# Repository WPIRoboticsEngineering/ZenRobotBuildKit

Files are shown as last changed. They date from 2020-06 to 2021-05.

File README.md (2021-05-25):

# ZenRobotBuildKit

Zen robotics build kit is a robot build system. Here are the BOM and CAD models.


 

# Set Up An IDE

Instructions for setting up an IDE will be provided in class.

# Build the Romi

Instructions will be provided in class.

# RBE1001Lib Documentation

[RBE1001Lib Doxygen page](https://wpiroboticsengineering.github.io/RBE1001Lib/annotated.html)

# BOM Source

## Tools Kit (Online only, suggested)
  
  1 x wire stripper https://www.pololu.com/product/1923
  
  1 x Digital Multi Meter https://www.sparkfun.com/products/12966
  
  1 x soldering iron  https://www.sparkfun.com/products/14456
  
  1 x soldering stand  https://www.sparkfun.com/products/9477
  
  1 x spool of solder lead free https://www.digikey.com/product-detail/en/aven-tools/17551LF/243-1341-ND/5252791
  
  1 x spool of solder wick https://www.sparkfun.com/products/9327
  
  1 x spring scale https://www.elexp.com/71ea7-g63spring-scale-tubular-5000g-yel.html
  
  1 x x86_64 PC running Windows or Linux nativly
  * No MacOS (install windows dual-boot)
  * No Chromebooks (No way to get the software working)
  * No Microsoft Surfaces (if they are the ARM variant)

## Consumables Kit 

  Note that students only need a portion of the items here: e.g., they don't each need a wire spool kit -- they just need enough wire to wire their 'bot.

  1 x pack of zipties https://www.amazon.com/Cable-Nylon-Locking-Pieces-Black/dp/B07VRSQ6YL
  
  1 x roll double sided tape Foam tape https://www.amazon.com/Scotch-Mounting-0-75-inch-350-inches-110-LongDC/dp/B009NP1OBC
  
  1 x Wire Kit https://www.amazon.com/REXQualis-Breadboard-Assorted-Prototyping-Circuits/dp/B081H2JQRV
  
  1 x Wire spool kit https://www.amazon.com/StrivedayTM-Solid-Electric-gauge-26-2ft/dp/B077HRKYB1
  
  ```alternate   https://www.mouser.com/ProductDetail/Adafruit/1311?qs=GURawfaeGuBbUKgxUfZ%252BxQ%3D%3D```

## ESP32 Processor Kit CD-2021

1 x ESP32-DevKitC-VB https://www.digikey.com/product-detail/en/espressif-systems/ESP32-DEVKITC-32D/1965-1000-ND/9356990

1 x ZenDriver board (Provided by B Star contract manufacturer) https://shop.bstarengineering.com/

1 x USB cable https://www.amazon.com/NetDot-Magnetic-Charging-Transfer-Compatible/dp/B07QDS3CHN bought in packs of 3

1 x Breadboard https://www.pololu.com/product/4000 (specifically this one, as it has mounting holes)

## ESP32 Processor Kit AB-2020

  1 x ESP32-DevKitC-VB https://www.digikey.com/product-detail/en/espressif-systems/ESP32-DEVKITC-32D/1965-1000-ND/9356990
  
  1 x USB cable https://www.amazon.com/NetDot-Magnetic-Charging-Transfer-Compatible/dp/B07QDS3CHN bought in packs of 3

  1 x Breadboard https://www.pololu.com/product/4000 (specifically this one, as it has mounting holes)
  
  1 x #3543 Motor Driver and Power Distribution Board for Romi Chassis = 19.95
  
  7 x Zener Diode https://www.digikey.com/products/en?keywords=BZX55B3V9-TAPGICT-ND
  
  3 x 1x06 Male Header https://www.digikey.com/products/en?keywords=2057-PH1-06-UA-ND
  
  2 x 1x03 Female Header https://www.digikey.com/product-detail/en/sullins-connector-solutions/PPPC031LFBN-RC/S7036-ND/810175
  
  2 x 1x04 Male Header https://www.digikey.com/products/en?keywords=%202057-PH1-04-UA-ND
  
  4 x 1x19 Female Header https://www.digikey.com/products/en?keywords=PPTC191LFBN-RC
  
  1 x 1x02 male header https://www.digikey.com/product-detail/en/adam-tech/PH1-02-UA/2057-PH1-02-UA-ND/9830266
  
  1 x 1x04 Female Header https://www.digikey.com/product-detail/en/sullins-connector-solutions/PPPC041LFBN-RC/S7037-ND/810176
  
  1 x 1x03 Male Header https://www.digikey.com/product-detail/en/sullins-connector-solutions/PREC003SAAN-RC/S1012EC-03-ND/2774851
  
  1 x Romi Battery Contact Set https://www.pololu.com/product/3540

  1 x 1 kOhm resistor (reassigned from Sensors Kit -- only needed for shim board)
  
  1 x jumper

  1 x Custom PCB https://github.com/WPIRoboticsEngineering/1001-romi-processor-shim
  
```
  This will be produced and provided by the Robotics Department 
  ```

## 32u4 Processor Kit

  1 x Romi 32U4 Control Board https://www.pololu.com/product/3544
  
  3 x 1x6 socket: https://www.pololu.com/product/1016
  
  2 x 1x9 socket: https://www.pololu.com/product/1019 (2001 students: you'll also need the 3rd 1x9 socket in the Sensors Kit.)
  
  1 x 1x40 breakaway pins: https://www.pololu.com/product/1065
  
  1 x USB cable https://www.amazon.com/NetDot-Magnetic-Charging-Transfer-Compatible/dp/B07QDS3CHN bought in packs of 3

  1 x Breadboard https://www.pololu.com/product/4000 (specifically this one, as it has mounting holes)
  
  1 x Side-entry screw terminal: https://www.pololu.com/product/2491 (comes in packs of three -- each kit needs one)

## Chassis Kit

  1 x #3660 Romi Chassis Kit/Encoders (BULK special purchase)
  ```
  Low volume alternate source 
  
   1 x chassis kit https://www.pololu.com/product/3501
   1 x Romi Encoder Pair https://www.pololu.com/product/3542
  
  ```
  
  1 x #3560 Romi Chassis Expansion Plate - Black = 4.75
  
  1 x #3531 Romi Chassis Ball Caster Kit = 2.95 (color unimportant)
  
  1 x #1944 Aluminum Standoff: 1 1/4", 2-56 thread (4-pack): https://www.pololu.com/product/1945
  
  1 x #1943 Aluminum Standoff: 3/4", 2-56 thread (4-pack): https://www.pololu.com/product/1943

  1 x #2009 Aluminum Standoff: 1 1/2", 2-56 thread (4-pack): https://www.pololu.com/product/2009
  
  1 x 2-56 nut set https://www.pololu.com/product/1067
  
  1 x 2-56 x 1/4"long https://www.pololu.com/product/1955   

  1 x Servo with feedback https://www.pololu.com/product/3436
  
  1 x 2-56x 1.25" https://www.mcmaster.com/90272A087
  
  10 x 2-56x 3/4" https://www.mcmaster.com/90272A084
  
## Sensors Kit
  
  1 x line sensor array (6 x 8mm): https://www.pololu.com/product/4246
  
  1 x ultrasonic https://www.sparkfun.com/products/15569 
  
  1 x wire for ultrasonic https://www.sparkfun.com/products/10369

  2 x photoresistor: https://www.sparkfun.com/products/9088
  
  1 x yellow LED
  
  1 x 330 Ohm resistor

  2 x 2.2 kOhm resistor
  
  (1) 1x9 socket: https://www.pololu.com/product/1019 
  
  1 x potentiometer Digikey PN 3310R-125-103L-ND
  
  1 x IR receiver: https://www.pololu.com/product/2471 

  1 x IR remote: https://www.pololu.com/product/2777
  
## 2001 Add On kit

 1 x Motor With Encoder https://www.sparkfun.com/products/16413
 
 1 x Motor Driver - Dual TB6612FNG https://www.sparkfun.com/products/14450
 
 1 x transistor Digikey https://www.digikey.com/en/products/detail/on-semiconductor/2N2222/33077
 
 1 x relay Electronix Express PN: 22RCLR5V
  
 1 x Diode digikey 	1N4007-TPMSTR-ND
 
## 2002 Add On Kit
 
 1 x Cable for Sharp IR sensor: https://www.sparkfun.com/products/13685
 
 1 x SharpIR bracket https://www.pololu.com/product/2677
 
 1 x SharpIR proximity sensor https://www.pololu.com/product/136
  
 <!--(tentative) 1 x ToF distance sensor: https://www.pololu.com/product/2490-->

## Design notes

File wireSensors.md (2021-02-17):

# Ultrasonic Range Finder

## V3 boards

The shim board comes with a 4-pin port for connecting your ultrasonic sensor. Using your 4-wire cable connect the sensor to the port. Common practice is to use green for GND and red for power, which matches nicely with the cable.

Unfortunately, due to an oversight (from a change in ESP32 version), the pins that are wired to the ultrasonic don't have the necessary functionality, so you'll need to add wires to connect pin 16 to pin 22 and pin 17 to pin 23. You can just use the sockets in the shim board.

## v2 boards

Vcc to 5vv/VUSB

Gnd to Gnd

Echo to One side of a 2.2k resistor

The other side of the 2.2k Resistor to GPIO 22

Trig to GPIO 23

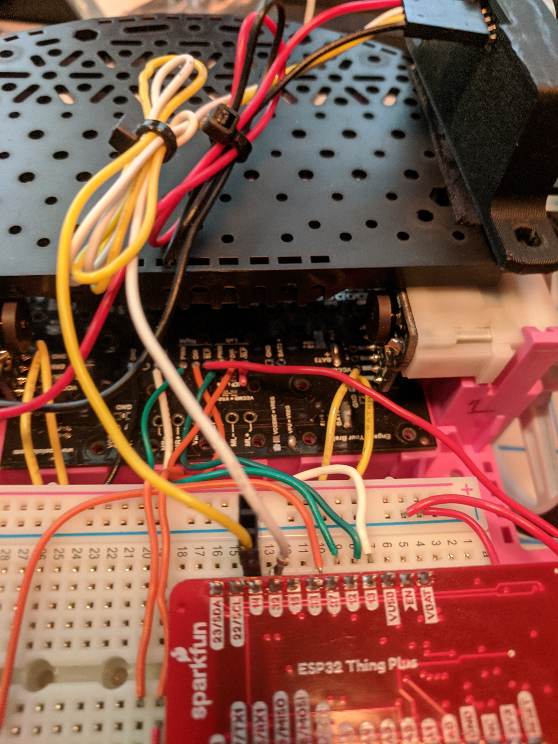
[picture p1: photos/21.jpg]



# Line Sensors

Your shim board has two 3-pin connectors for line sensors. The arrangement is set up to work with individual line sensors, but it will also work with the line sensor array.

Connect the '3V' terminal from one of the line sensor sockets to Vcc on the sensor array. Connect 'GND' to GND. You do not need to connect the '3V' and 'GND' from the other set of pins.

Connect the middle pin of each 3-pin socket to your choice of sensor elements: labelled 1, 3, 5, 7, 9, or 11 on the sensor array. These correspond to each of the physical sensors on the working side of the sensor array. In the end, you'll want to choose two sensors that are roughly the width of the piece of tape you use for line following, but you can easily try different sensor elements. The sockets are connected to pins 36 (A4) and 39 (A3) on your ESP32.

# Servo

The shim board has a 4-pin connector for the servo. Connect the black wire (ground) on the servo cable to the '-' terminal. The red wire will connect to 5V and the white to the signal line (pin 33). Connect the green feedback wire to the last pin, pin 34 (A2).

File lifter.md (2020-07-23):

# Build the Lift mechanism

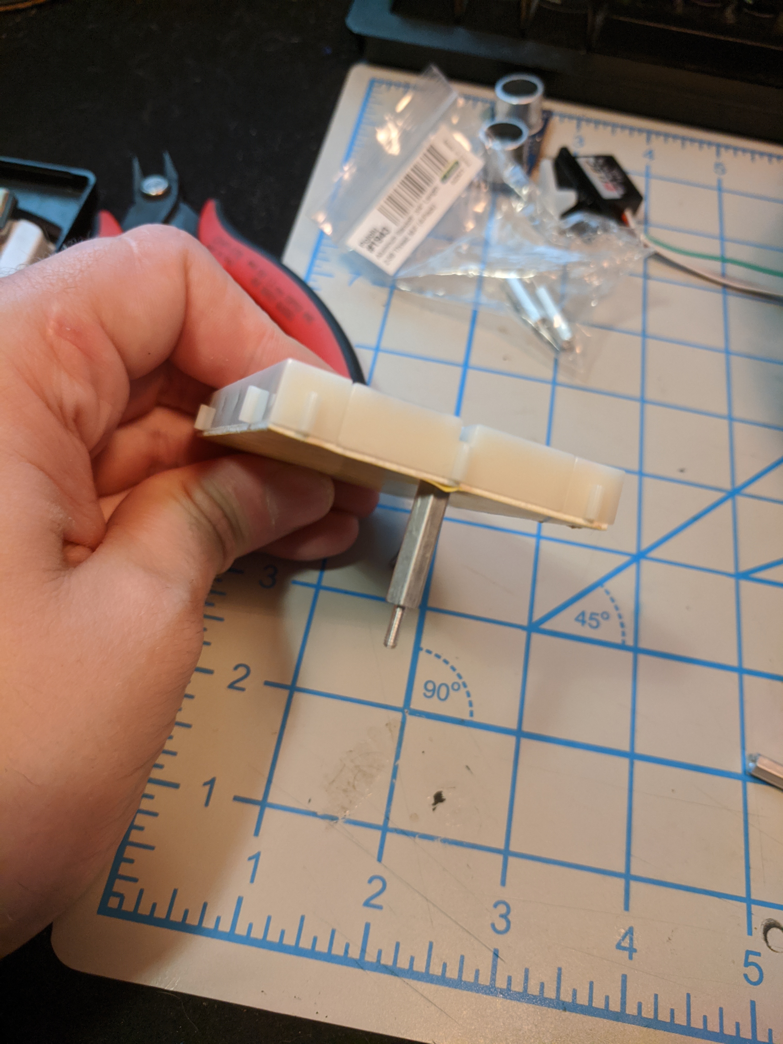
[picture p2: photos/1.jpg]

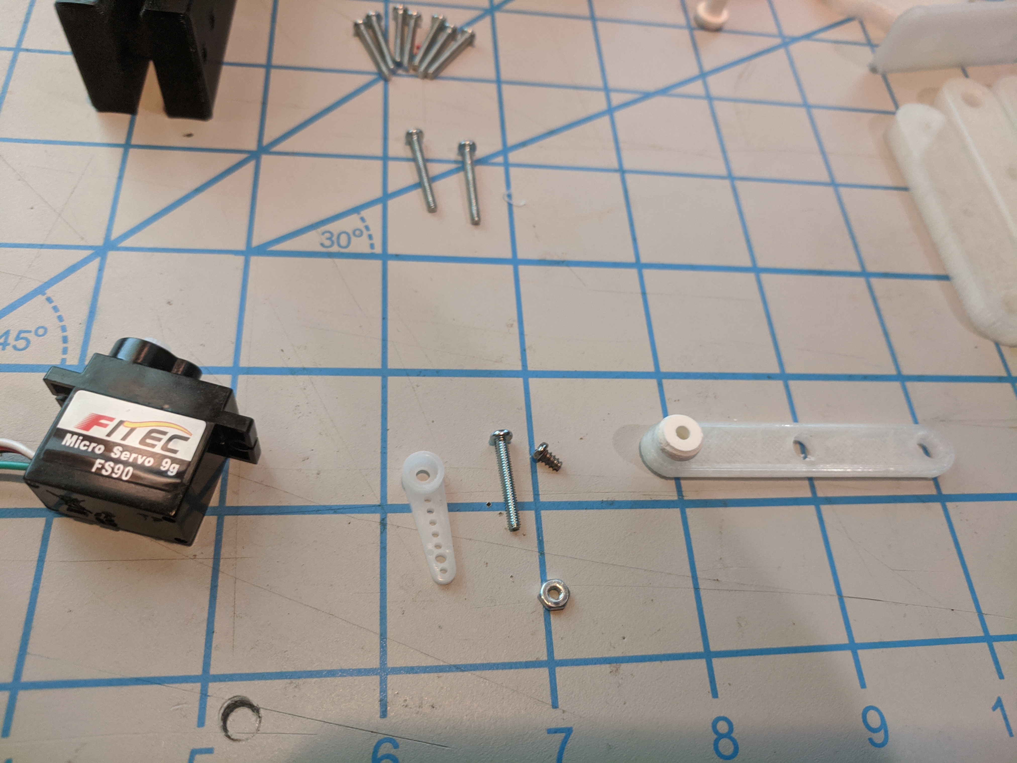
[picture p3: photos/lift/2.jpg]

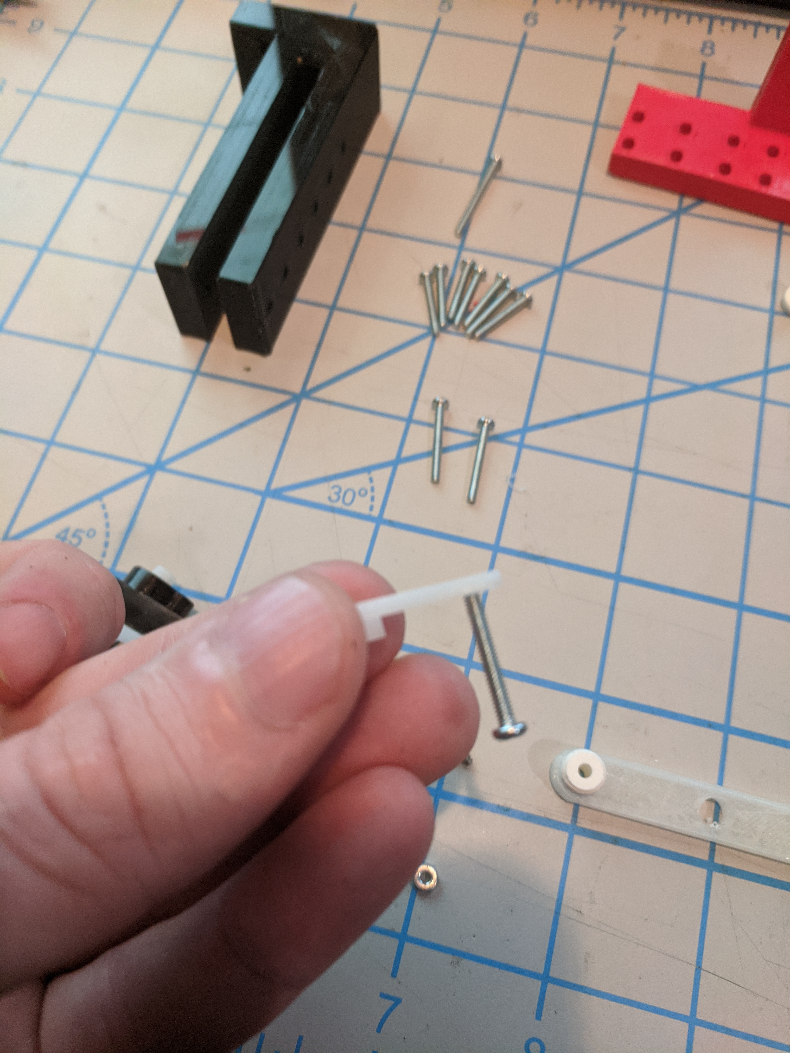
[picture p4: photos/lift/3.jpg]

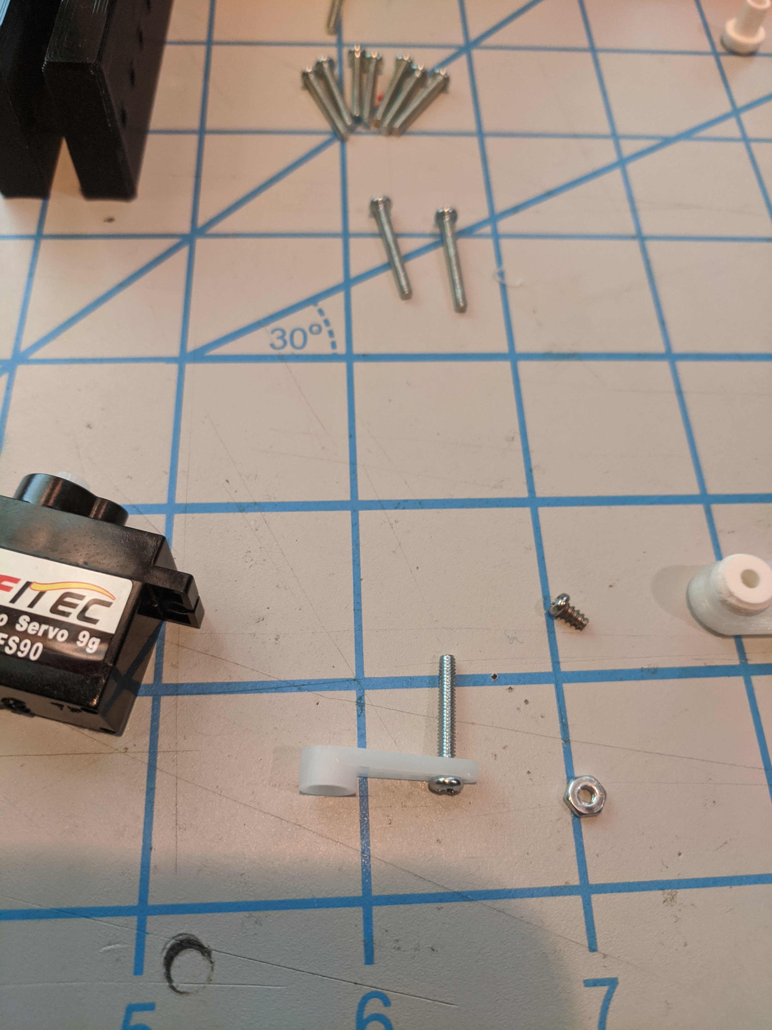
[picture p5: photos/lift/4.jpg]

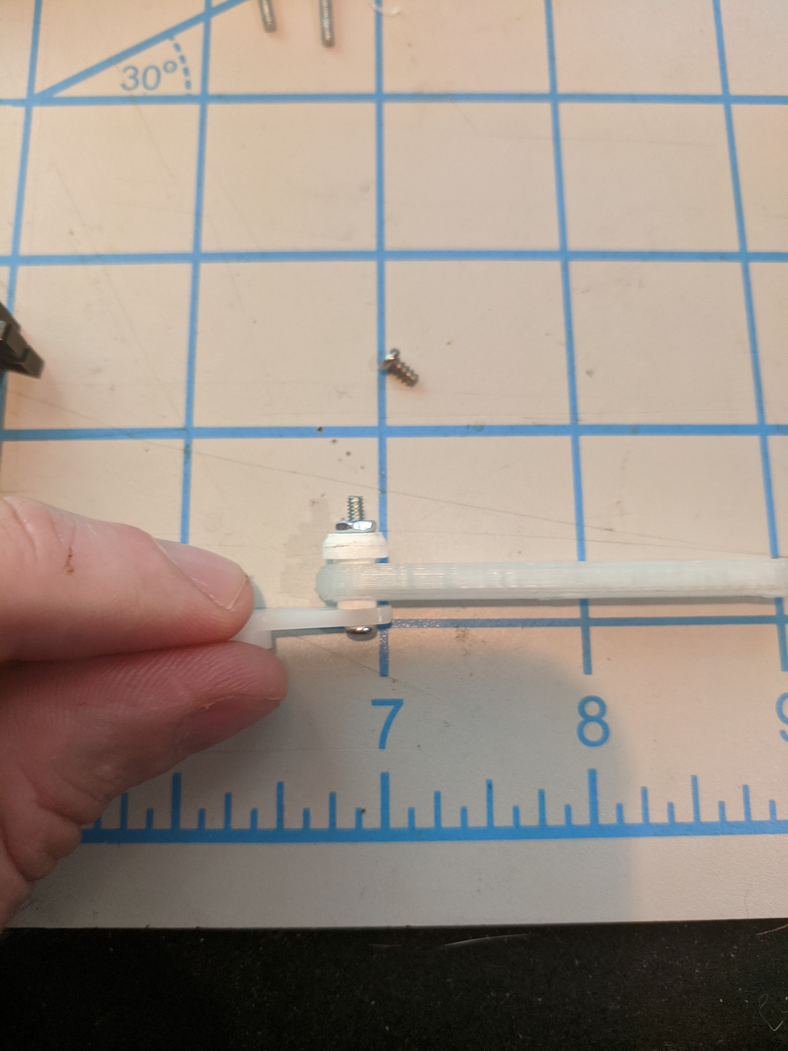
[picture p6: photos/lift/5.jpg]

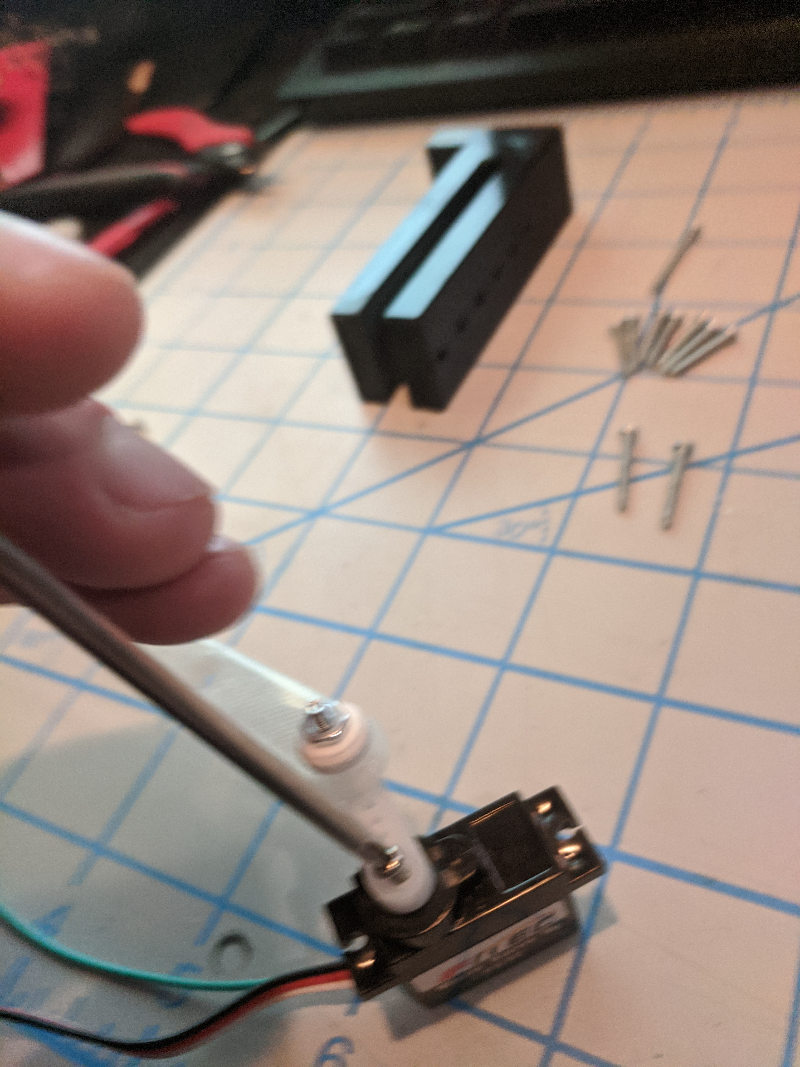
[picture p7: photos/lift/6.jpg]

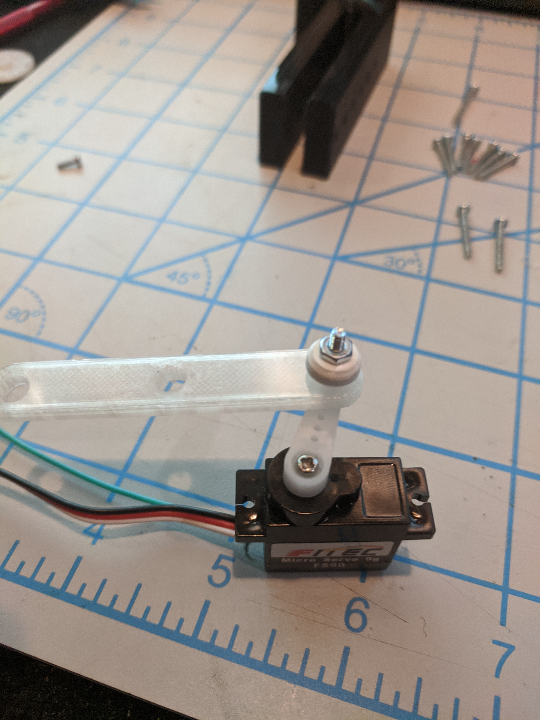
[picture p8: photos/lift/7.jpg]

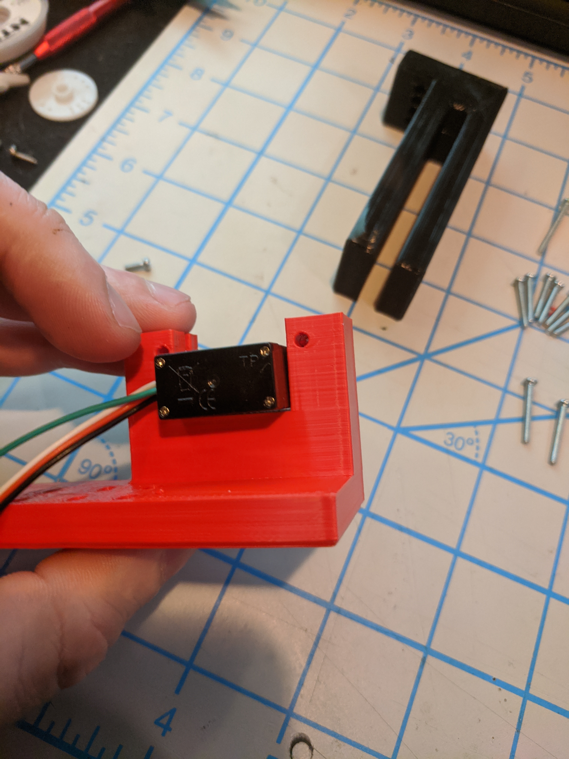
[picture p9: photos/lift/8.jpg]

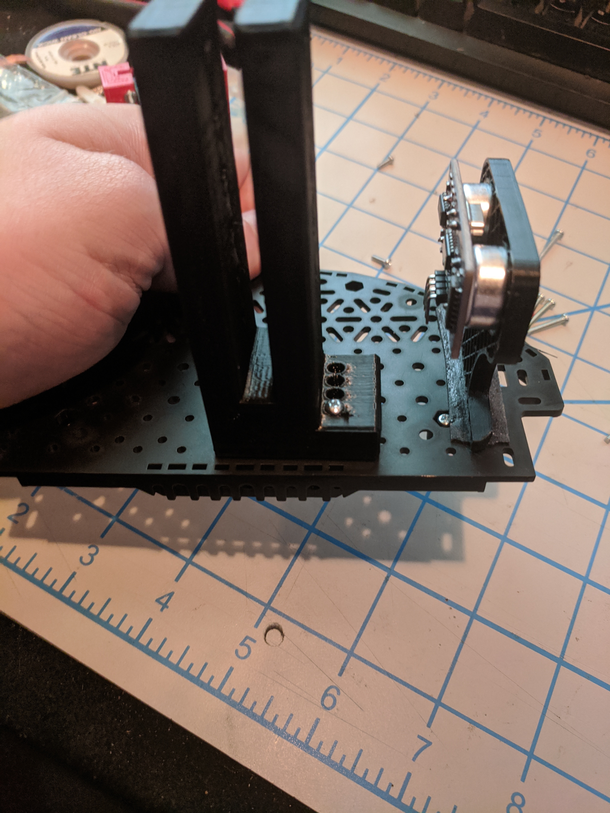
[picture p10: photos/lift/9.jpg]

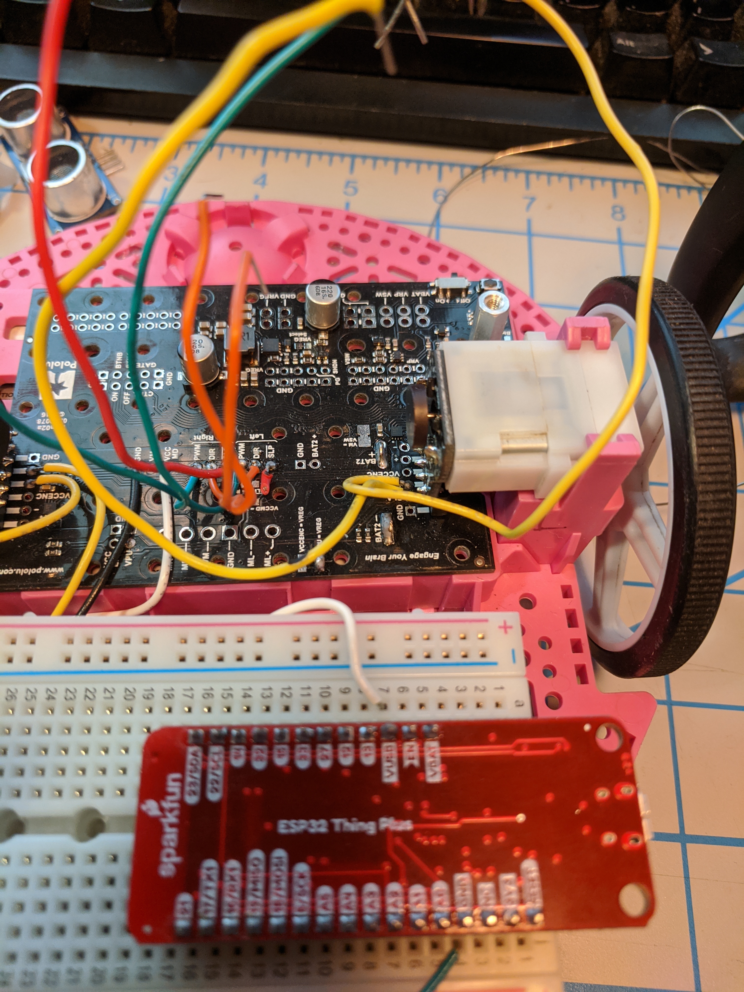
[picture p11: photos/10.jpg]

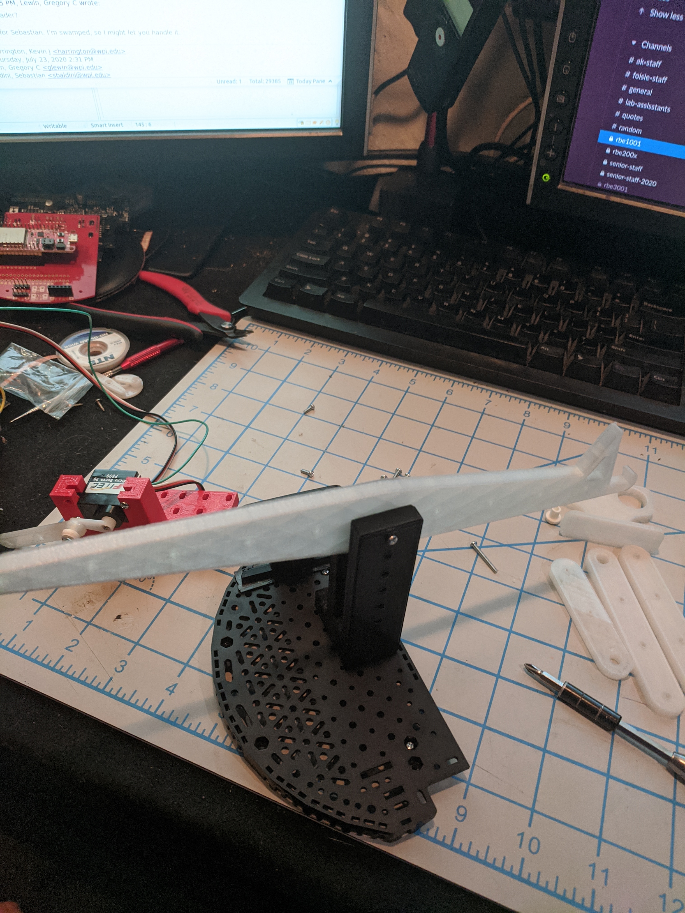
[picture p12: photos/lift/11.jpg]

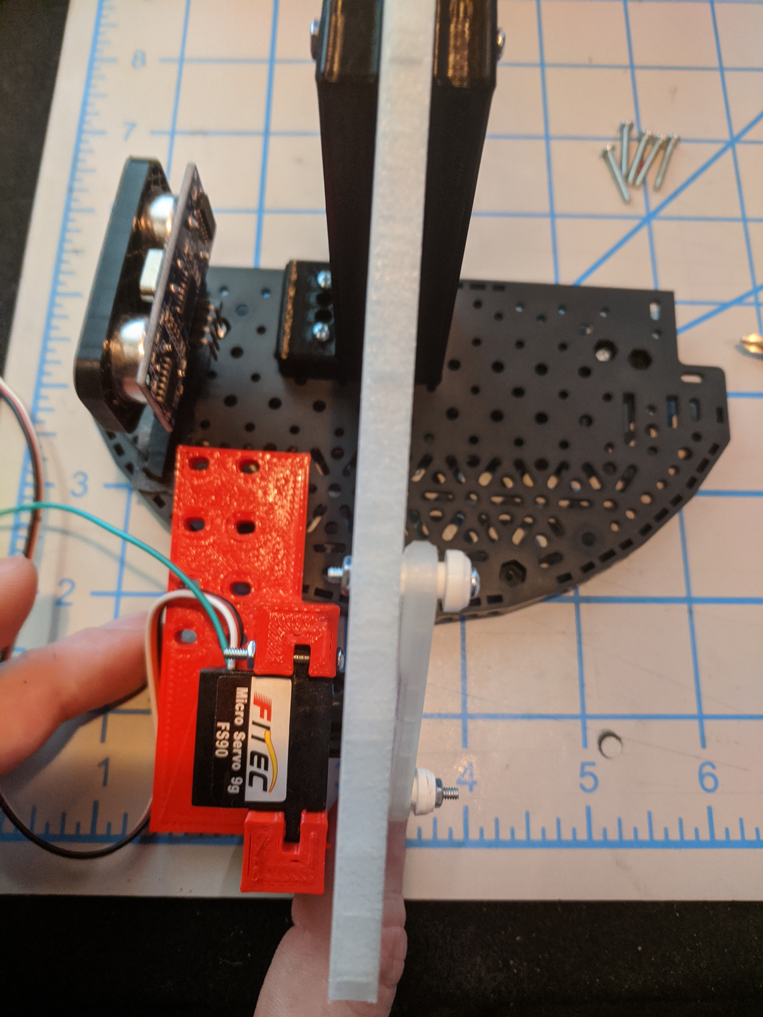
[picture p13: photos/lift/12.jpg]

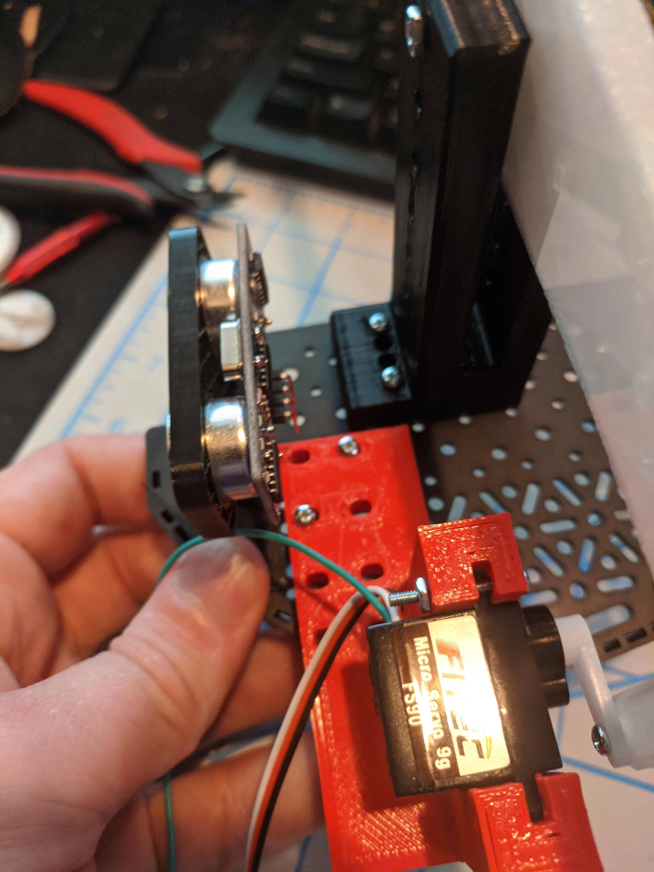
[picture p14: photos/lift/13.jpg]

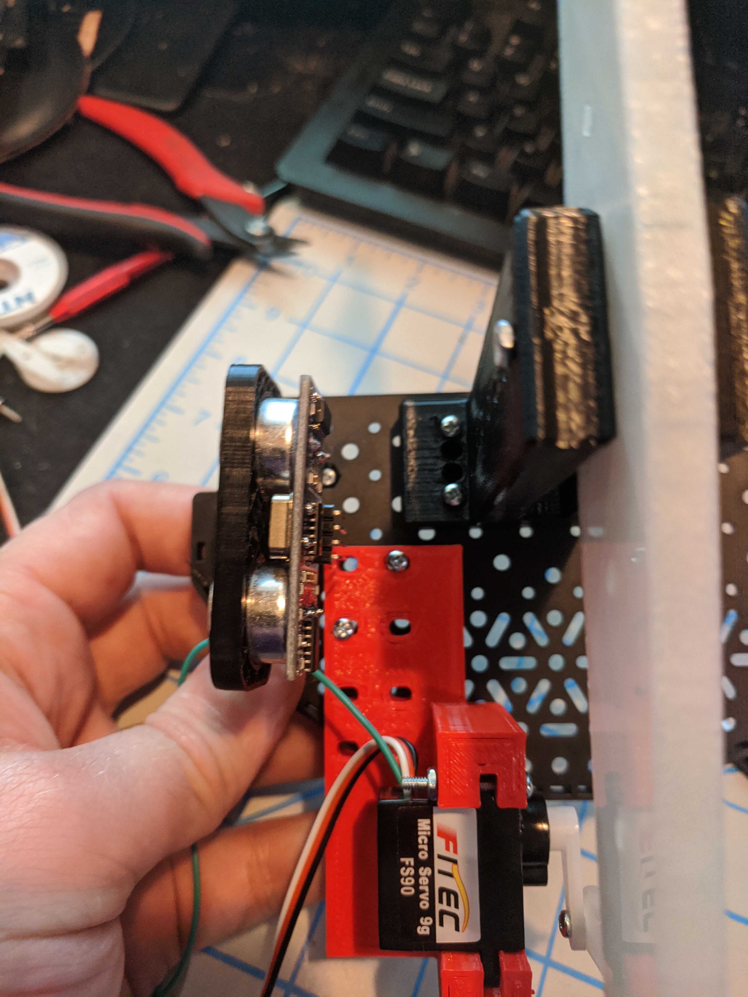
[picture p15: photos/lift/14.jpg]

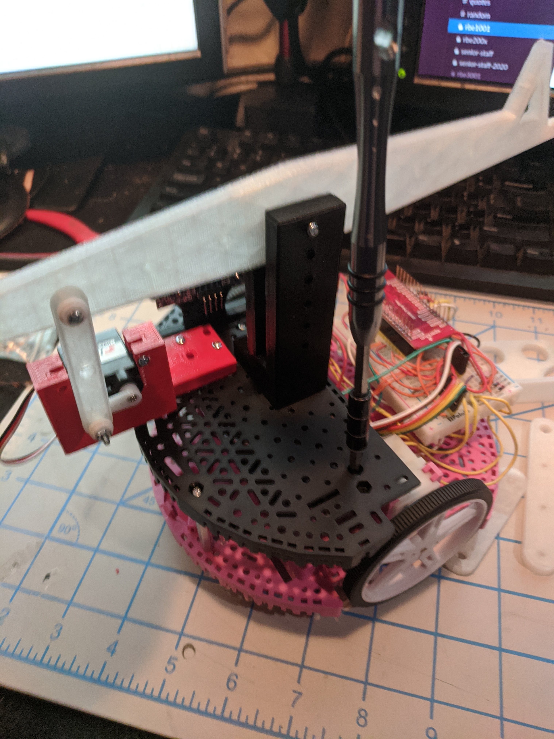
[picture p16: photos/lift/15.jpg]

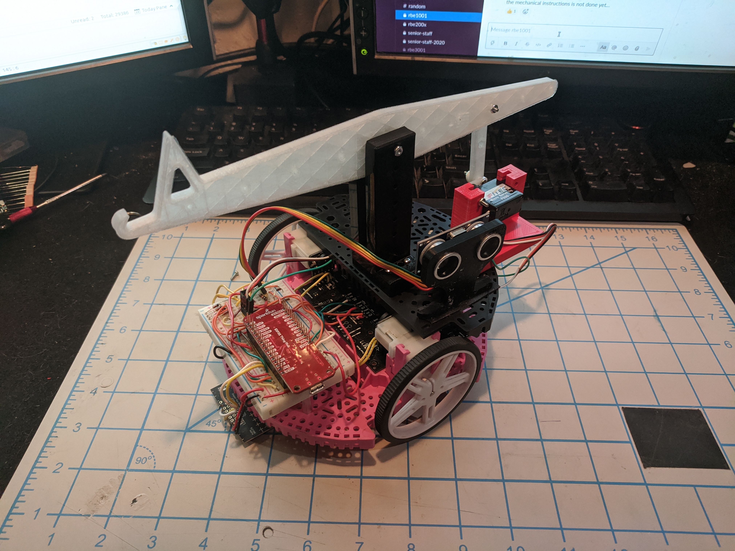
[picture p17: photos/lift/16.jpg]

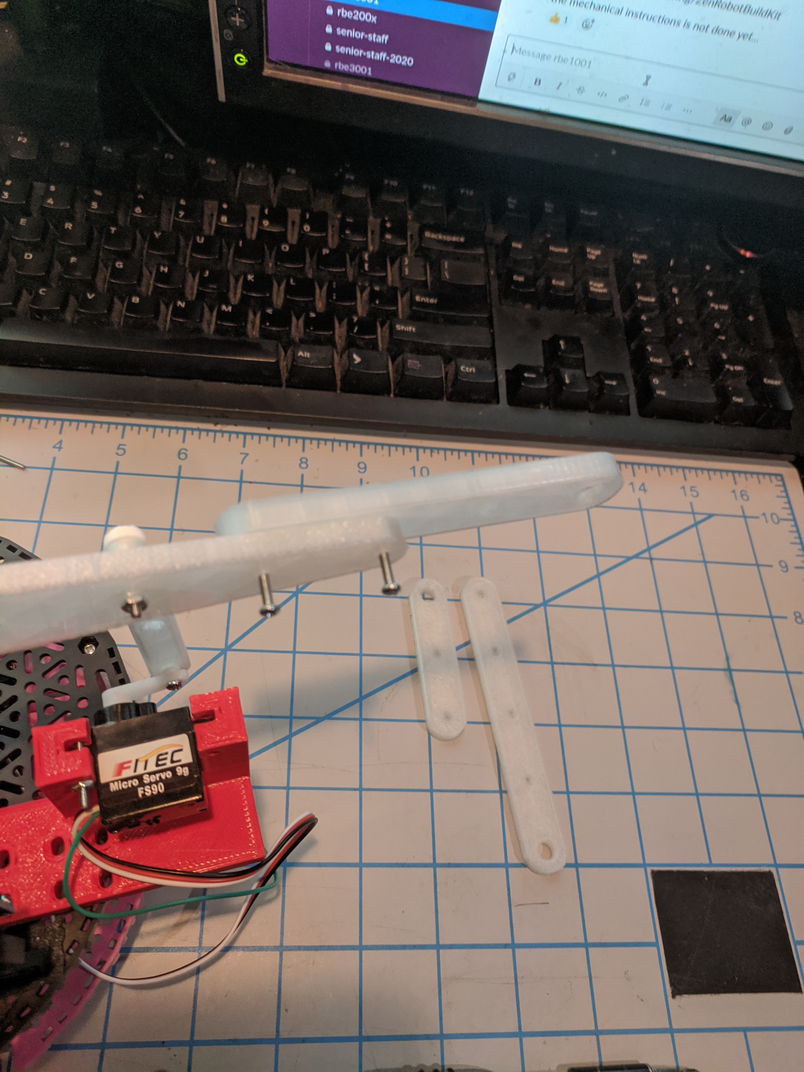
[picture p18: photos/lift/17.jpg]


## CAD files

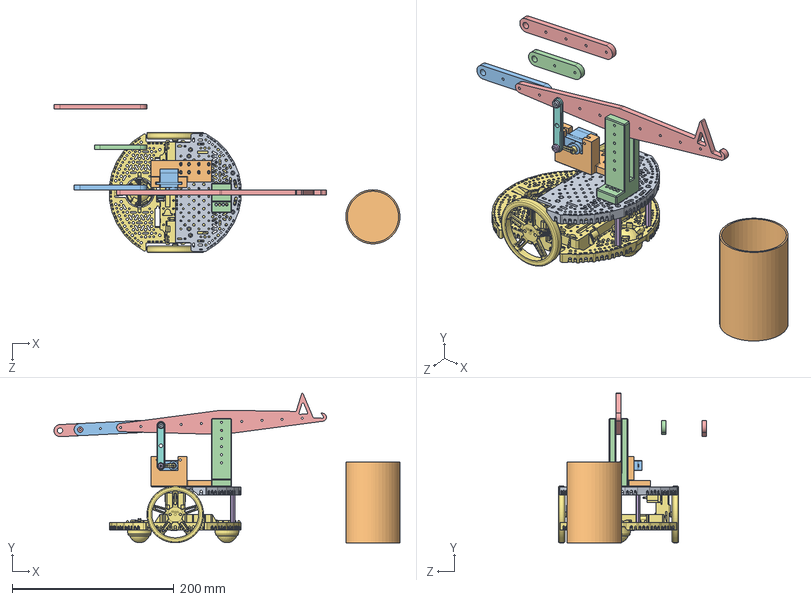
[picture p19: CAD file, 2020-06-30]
ServoCADModel/Romi/Servo Assembly.SLDASM
428.0 x 185.1 x 183.4 mm
romi-chassis-expansion-plate
ServoBracket
FS09R_Servo_Motor
Arm Bracket
arm2
38 mm Standoff x 2
romi-chassis-kit.step
Servo Link 50 mm
Link Bushing_2
Can
Counter Balance Arm 75
Counter Balance Arm 50
Counter Balance Arm 100
Link Bushing_1
servo horn 1 v2

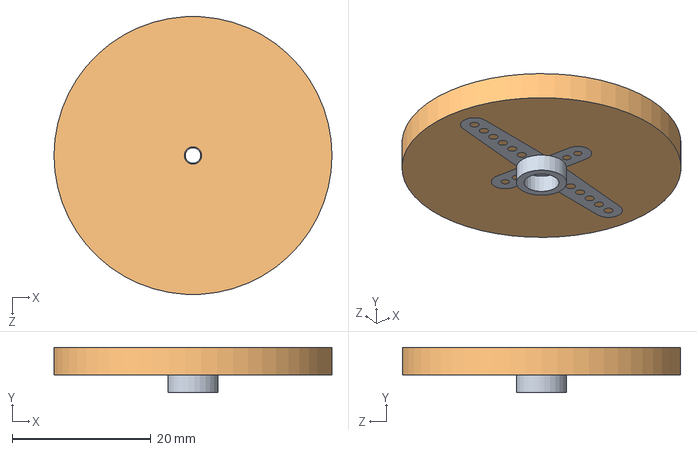
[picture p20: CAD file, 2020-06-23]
ServoCADModel/Romi/Servo Assembly/Horn Assembly.SLDASM
40.0 x 6.50 x 39.9 mm
servo horn 3 v1 cover
servo horn 3 v1 cover mold

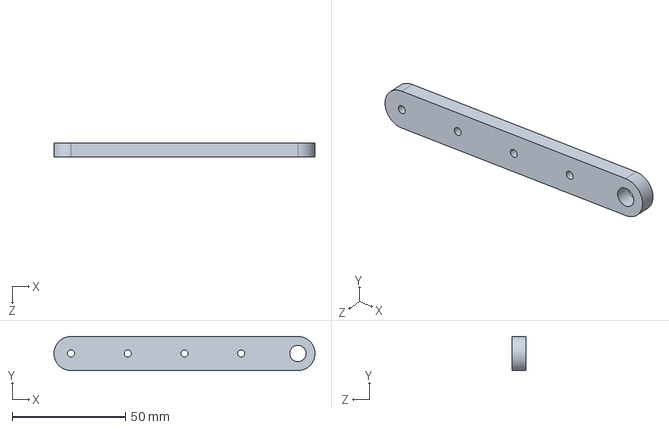
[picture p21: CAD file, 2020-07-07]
ServoCADModel/Romi/Counter Balance Arm 100.SLDPRT
115.0 x 15.0 x 6.00 mm

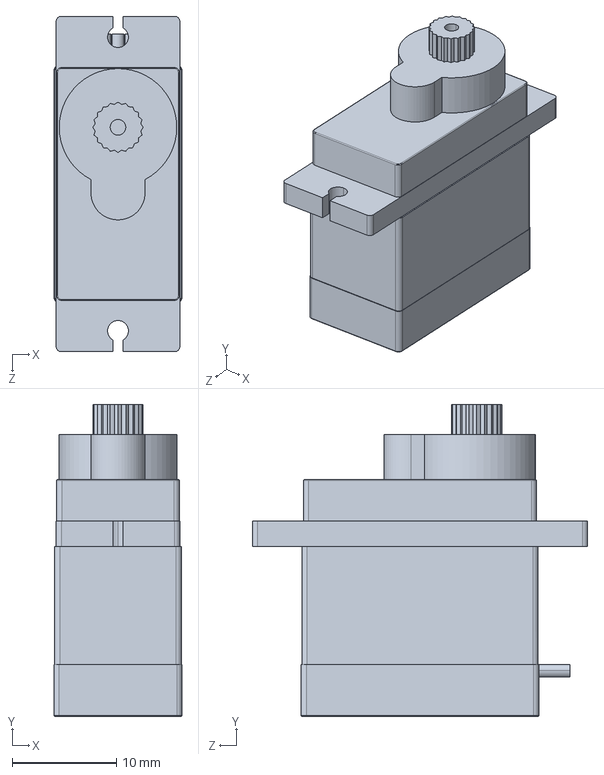
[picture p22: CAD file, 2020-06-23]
ServoCADModel/Romi/fs90r-continuous-rotation-servo-original-size-1.snapshot.7/FS09R_Servo_Motor.STEP
12.3 x 30.0 x 32.2 mm

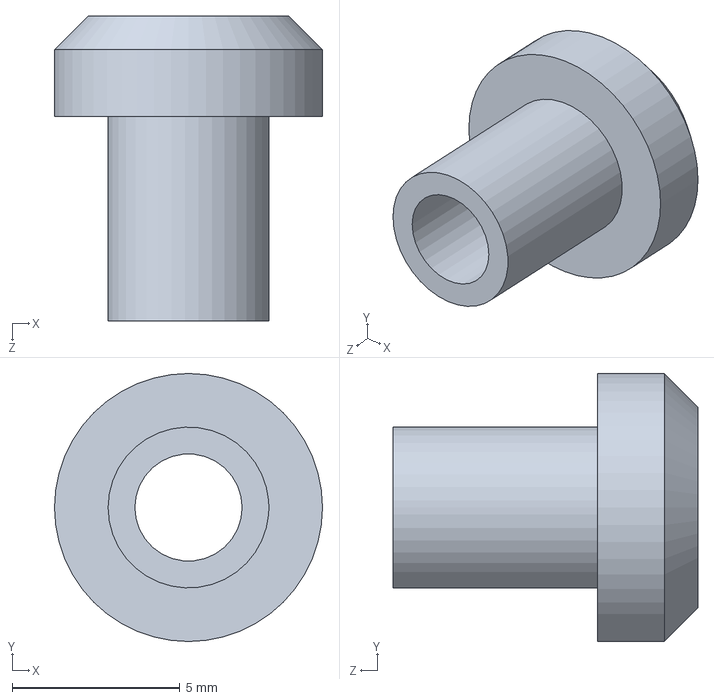
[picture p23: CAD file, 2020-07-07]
ServoCADModel/Romi/Servo Assembly/Link Bushing_1.SLDPRT
8.00 x 8.00 x 9.10 mm

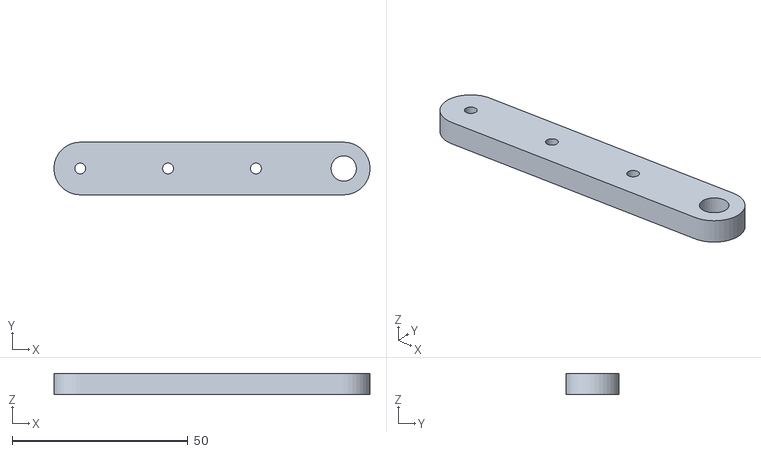
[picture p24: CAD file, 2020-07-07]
ServoCADModel/Romi/Servo STLs/Counter Balance Arm 75.STL
89.9 x 15.0 x 6.00

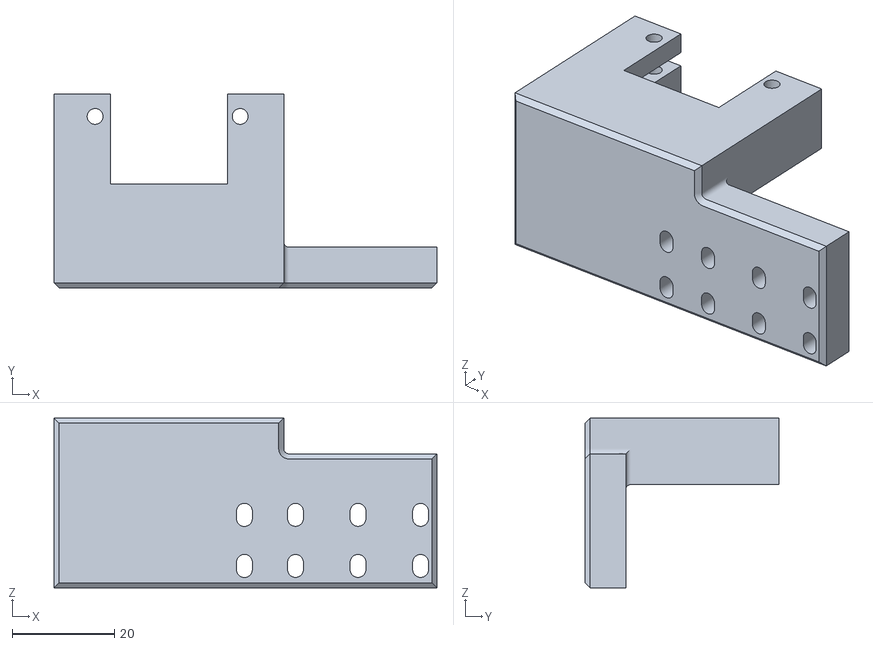
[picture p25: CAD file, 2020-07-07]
ServoCADModel/Romi/Servo STLs/ServoBracket.STL
75.0 x 38.0 x 33.2

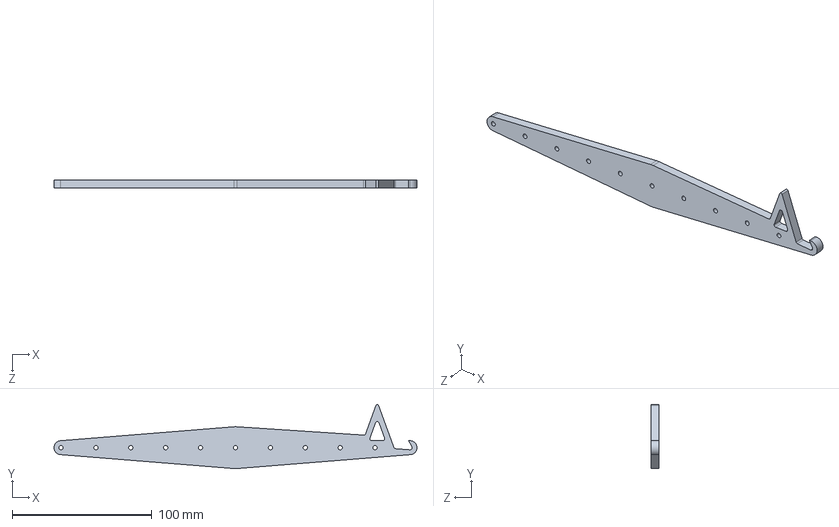
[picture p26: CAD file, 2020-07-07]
ServoCADModel/Romi/arm2.SLDPRT
260.0 x 46.0 x 6.00 mm

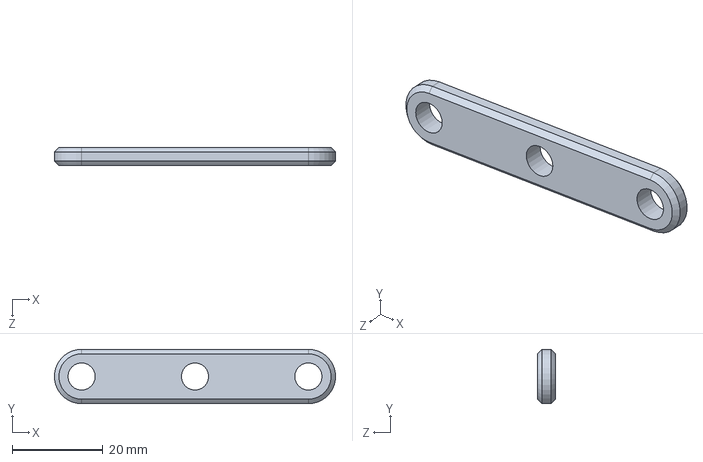
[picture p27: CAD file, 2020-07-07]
ServoCADModel/Romi/Servo Assembly/Servo Link 50 mm.SLDPRT
61.9 x 12.0 x 4.00 mm

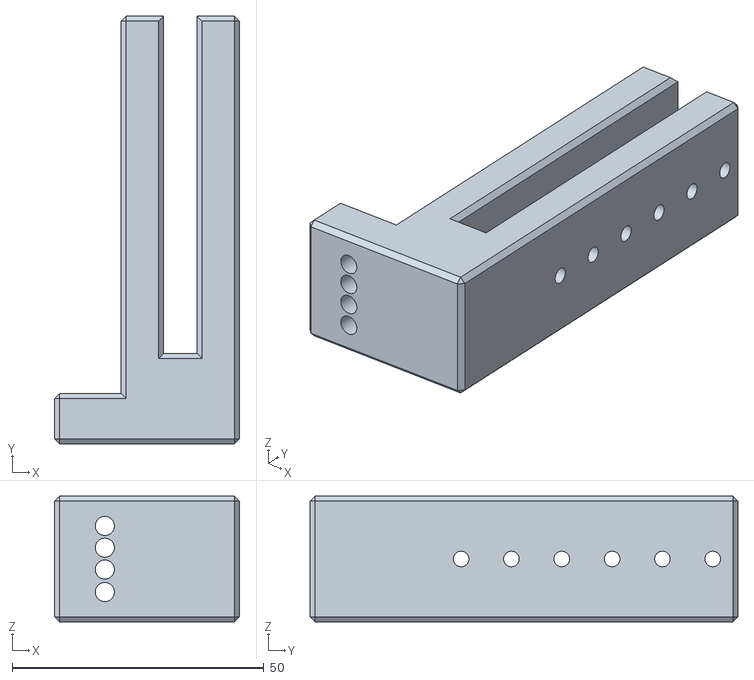
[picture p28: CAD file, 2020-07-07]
ServoCADModel/Romi/Servo STLs/Arm Bracket.STL
36.8 x 85.0 x 25.0

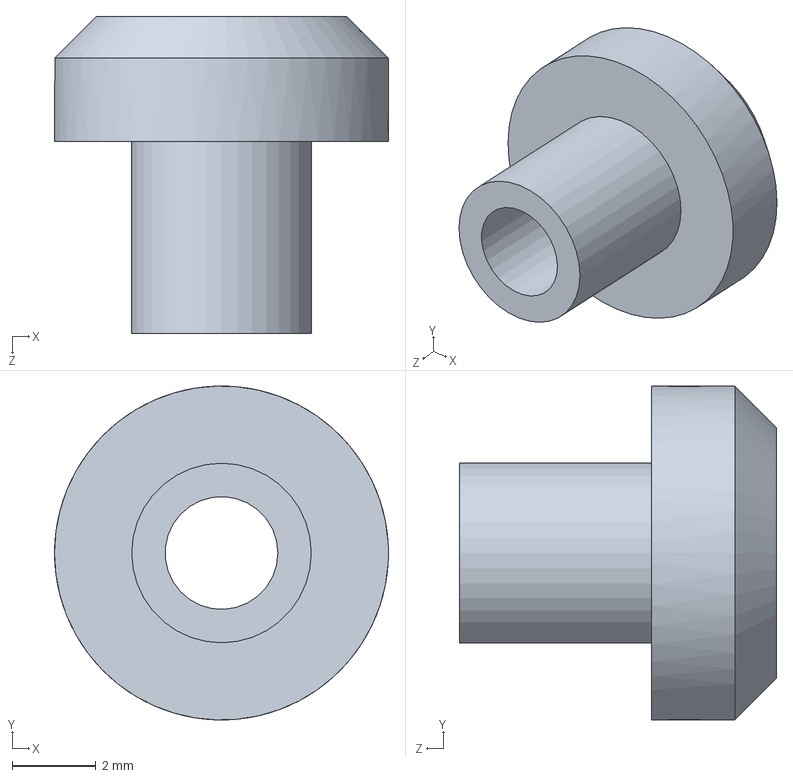
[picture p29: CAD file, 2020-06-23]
ServoCADModel/Romi/Servo Assembly/Link Bushing.SLDPRT
8.00 x 8.00 x 7.60 mm

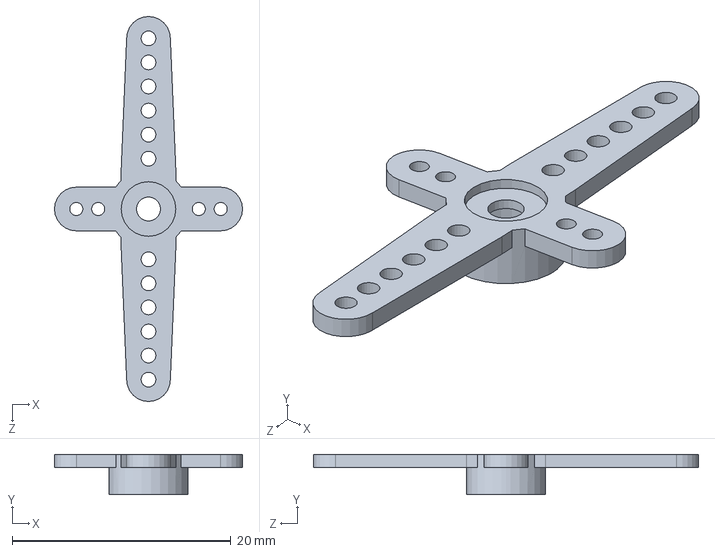
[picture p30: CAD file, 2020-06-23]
ServoCADModel/Romi/Servo Assembly/servo horn 3 v1.SLDPRT
17.2 x 3.70 x 35.2 mm

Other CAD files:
ServoCADModel/Romi/romi-chassis-kit.step.SLDASM
ServoCADModel/Romi/Servo Assembly/Link Bushing_2.SLDPRT
ServoCADModel/Romi/ServoBracket.SLDPRT
ServoCADModel/Romi/Counter Balance Arm 75.SLDPRT
ServoCADModel/Romi/Servo STLs/Servo Link 50 mm.STL
ServoCADModel/Romi/Arm Bracket.SLDPRT
ServoCADModel/Romi/Counter Balance Arm 50.SLDPRT
ServoCADModel/Romi/Servo Assembly/38 mm Standoff.SLDPRT
ServoCADModel/Romi/Servo Assembly/Arm Bracket.SLDPRT
ServoCADModel/Romi/Servo Assembly/Can.SLDPRT
ServoCADModel/Romi/Servo Assembly/FS09R_Servo_Motor.SLDPRT
ServoCADModel/Romi/Servo Assembly/ServoBracket.SLDPRT
ServoCADModel/Romi/Servo Assembly/romi-chassis-expansion-plate.SLDPRT
ServoCADModel/Romi/Servo Assembly/romi-chassis-expansion-plate.step
ServoCADModel/Romi/Servo Assembly/servo horn 1 v2.SLDPRT
ServoCADModel/Romi/Servo Assembly/servo horn 1 v2.step
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

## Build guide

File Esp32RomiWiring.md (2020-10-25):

# Step 0 Learn to Solder (Click on image to play on YouTube)

(https://www.youtube.com/watch?v=FWBCbFPXJLg)

# Step 1 Lay out your electronics

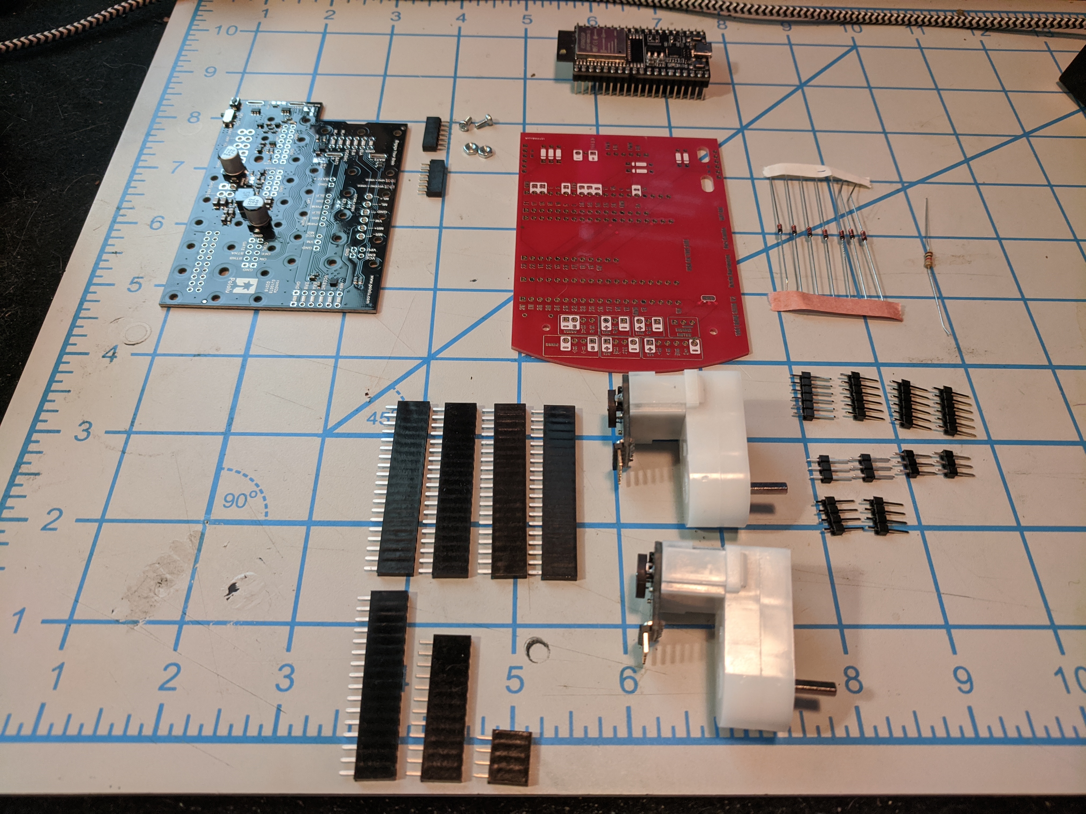
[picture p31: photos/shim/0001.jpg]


# Step 2 Solder in the 10k Resistor

All components -- resistors, diodes, and sockets -- go on the top (silk screen) side of the shim board. 

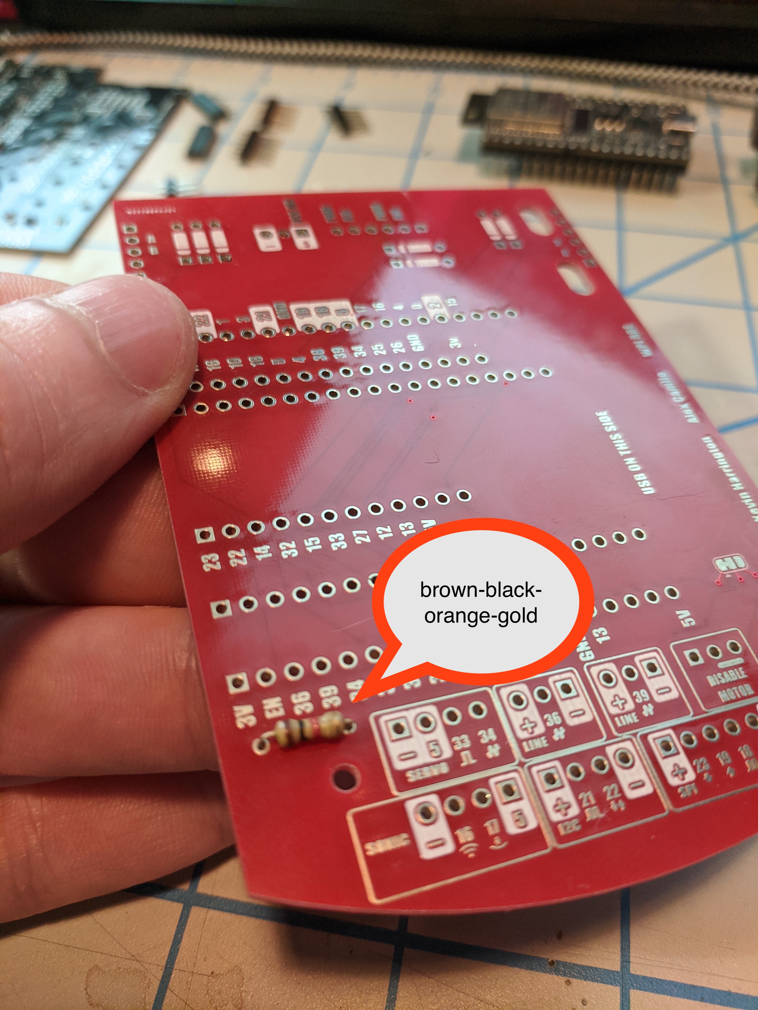
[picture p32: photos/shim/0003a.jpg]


Solder them from the bottom.

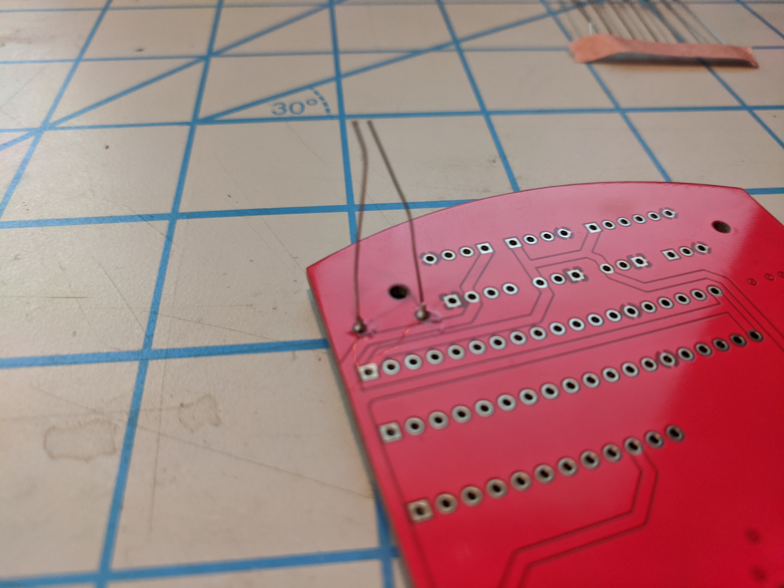
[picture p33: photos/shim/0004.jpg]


# Step 3 Solder in the Diodes

BE CAERFUL to line up the black stripe with the stripe in the silk screen. 

They are made of a bead of glass, be very careful with them.

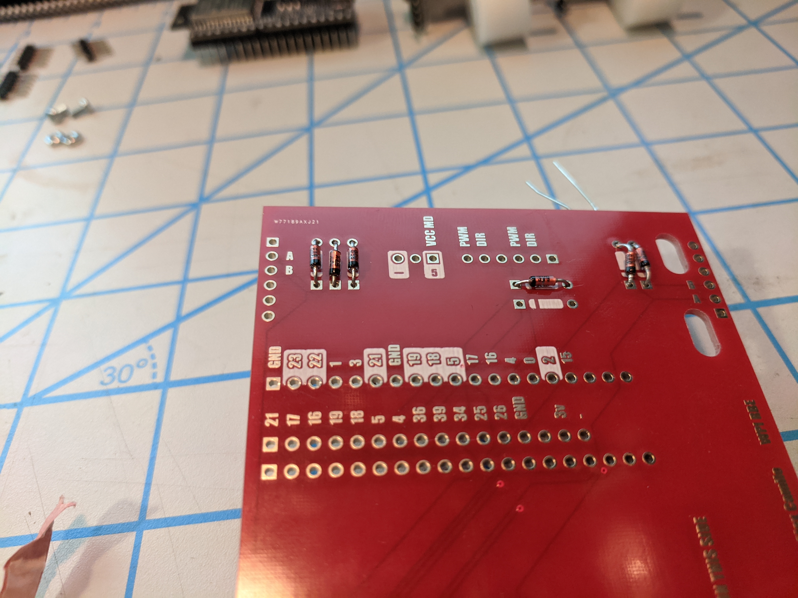
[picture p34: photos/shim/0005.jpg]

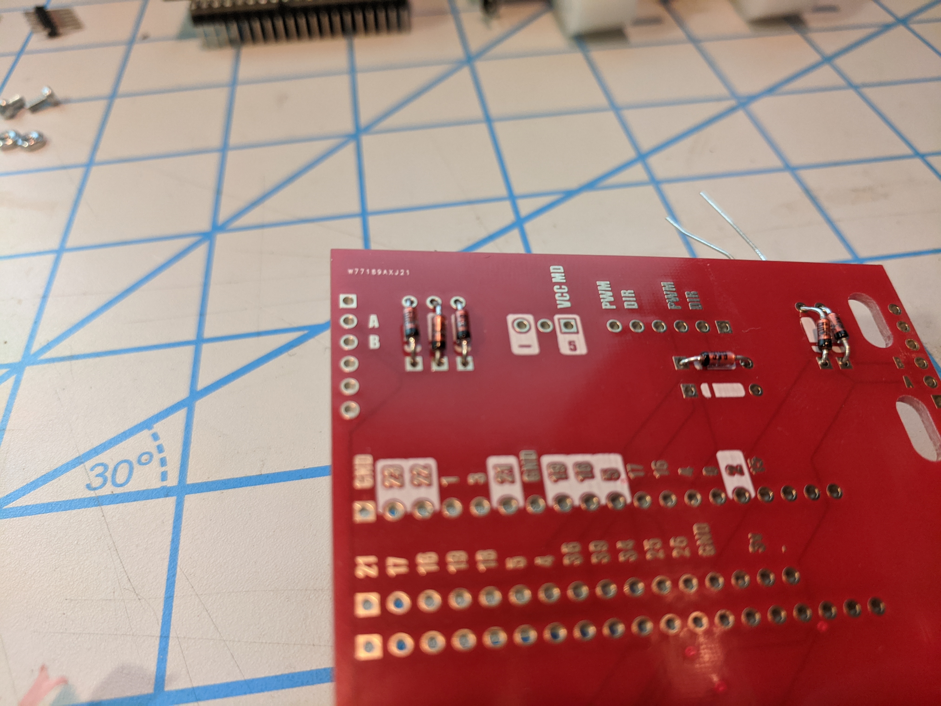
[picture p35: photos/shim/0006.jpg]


# Step 4 Solder the ESP32 Sockets

Start by placing the sockets on your processor

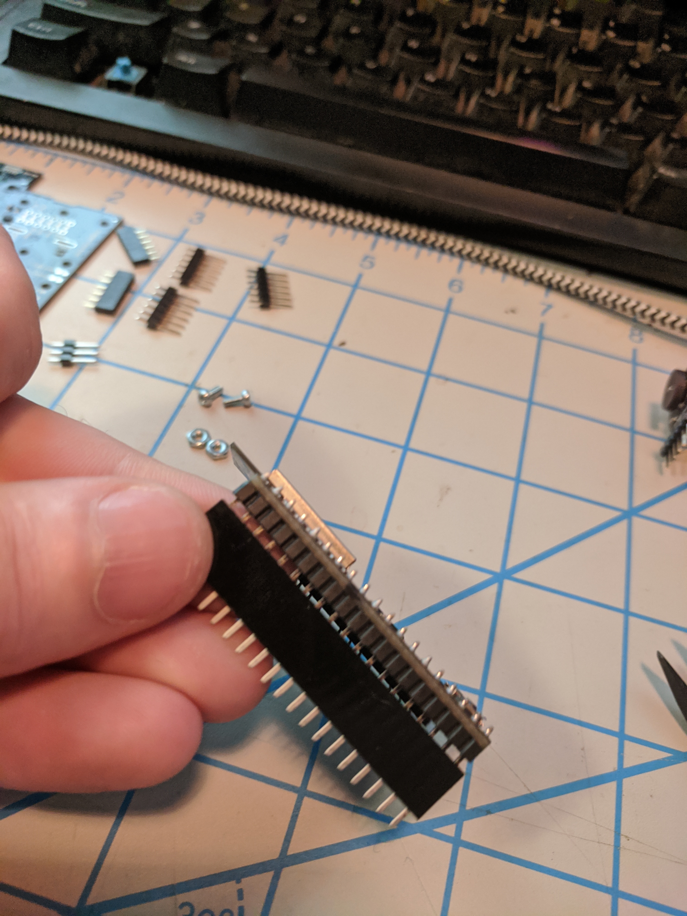
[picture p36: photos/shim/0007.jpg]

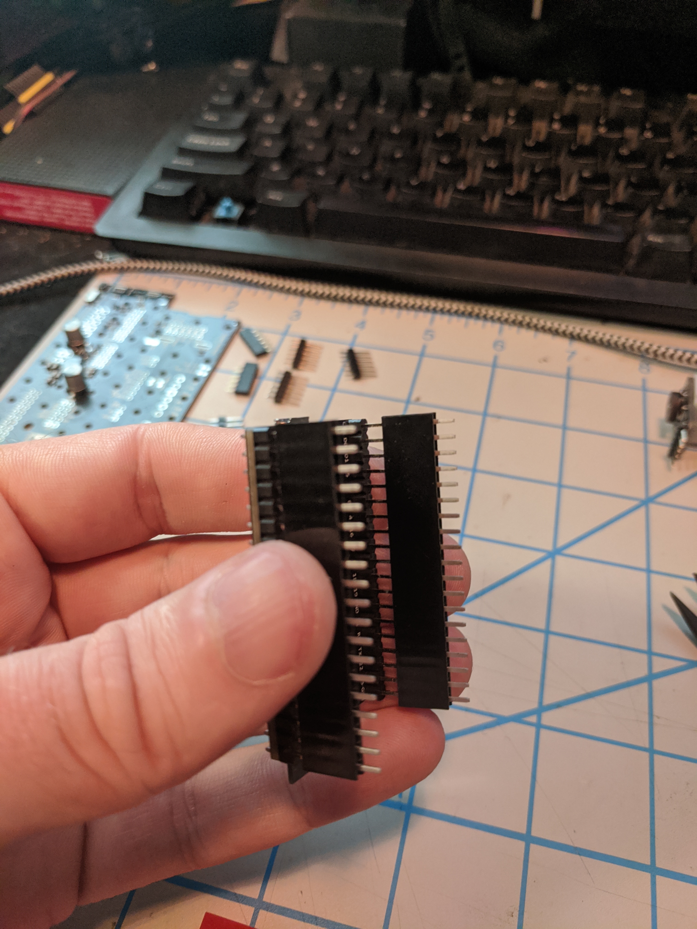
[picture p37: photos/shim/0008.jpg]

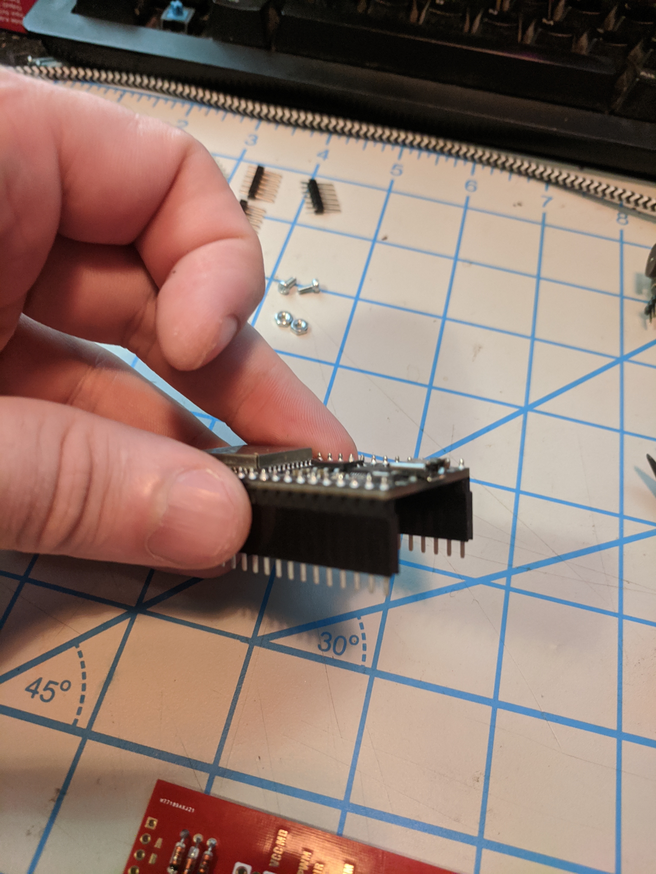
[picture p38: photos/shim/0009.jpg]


then insert the sockets into the Shim.

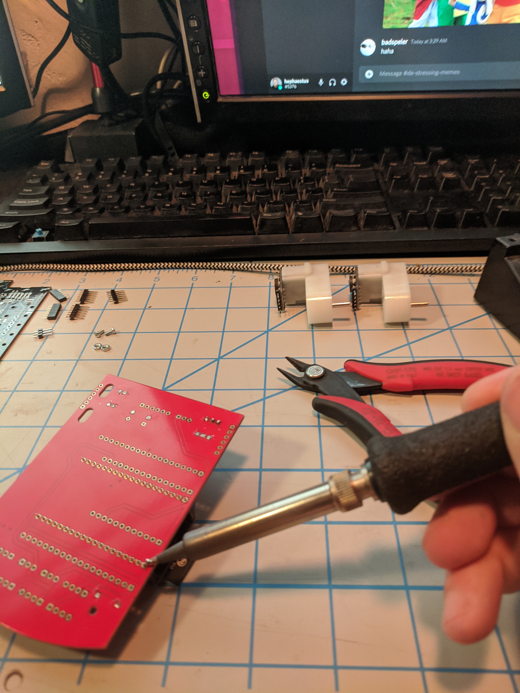
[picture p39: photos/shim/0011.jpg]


Flip it over and solder the pins



# Step 5 Solder the rest of the headers as shown

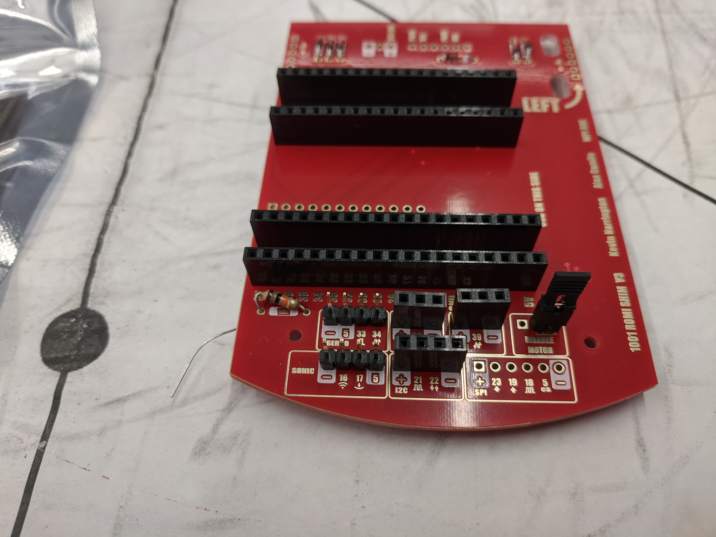
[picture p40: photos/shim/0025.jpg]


# Step 6 Solder the headers that come with the Driver Board

When soldering in the 1x6 sockets, be sure to use the short ones that came in the bag with the Driver Board. Be sure that the sockets are fully seated on the board and perpendicular to it; otherwise, you will have trouble connecting the motors later. Best to solder one connection and then check before you solder the other five.

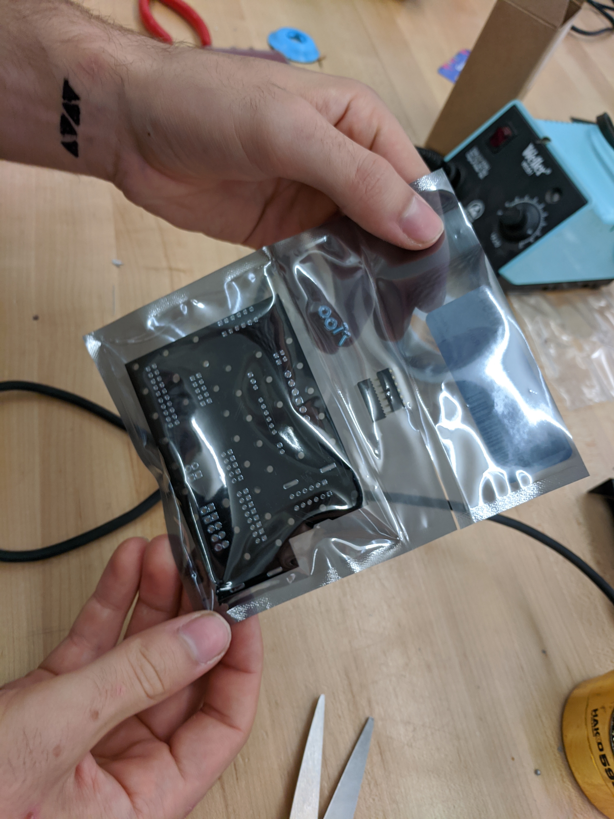
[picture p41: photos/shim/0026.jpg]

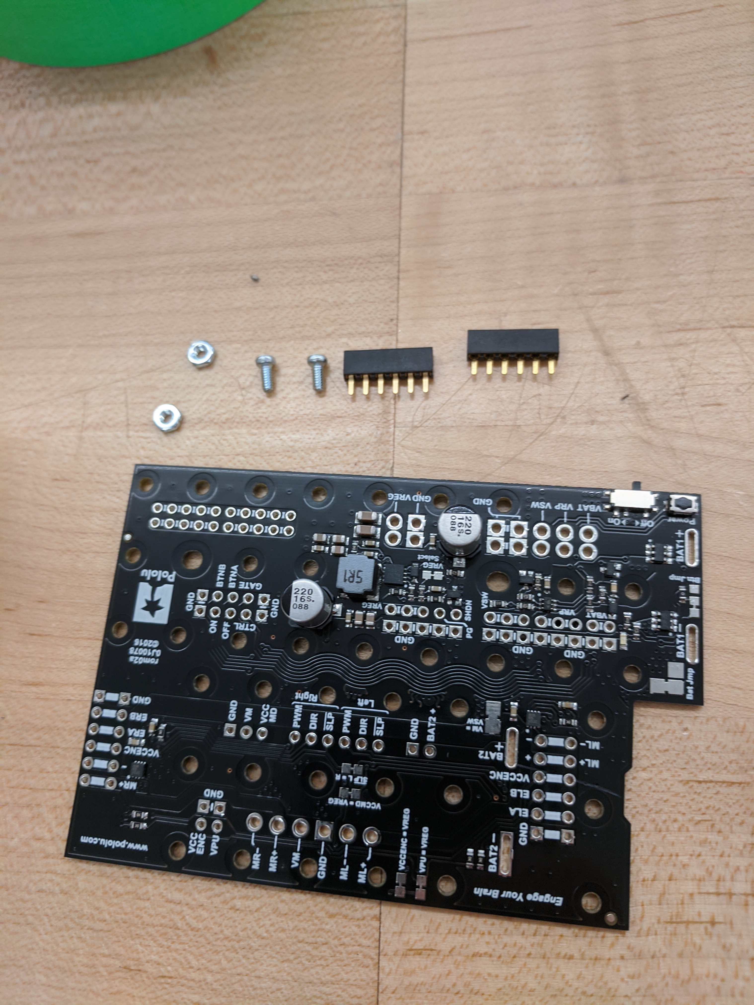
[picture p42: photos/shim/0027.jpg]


The sockets go in the outer positions.

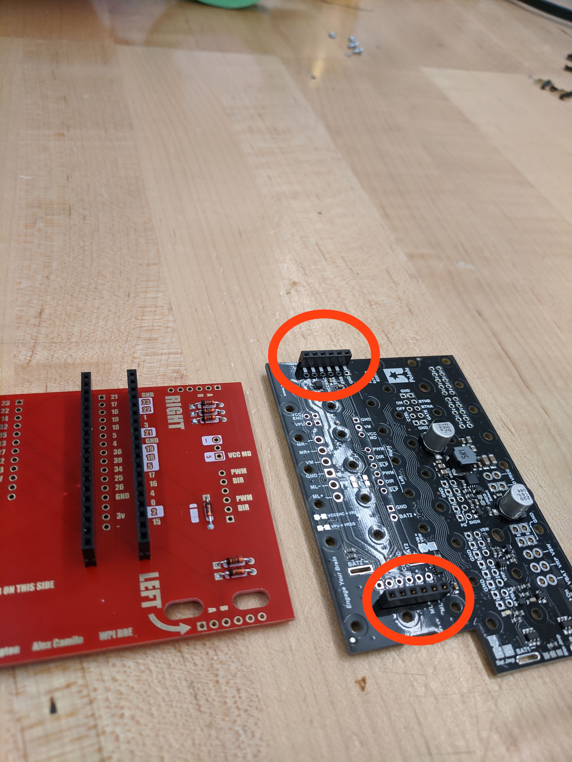
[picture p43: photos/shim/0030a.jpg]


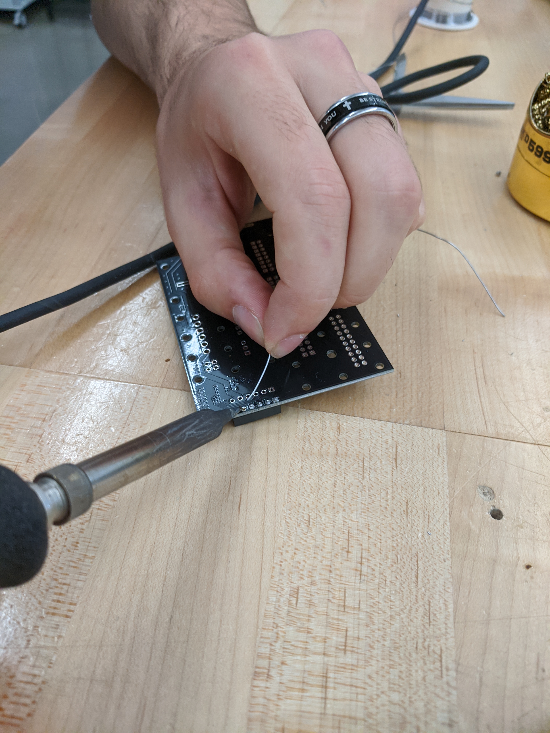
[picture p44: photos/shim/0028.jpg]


# Step 7 Dry fit the headers between the Driver and the Shim

Start with both boards.

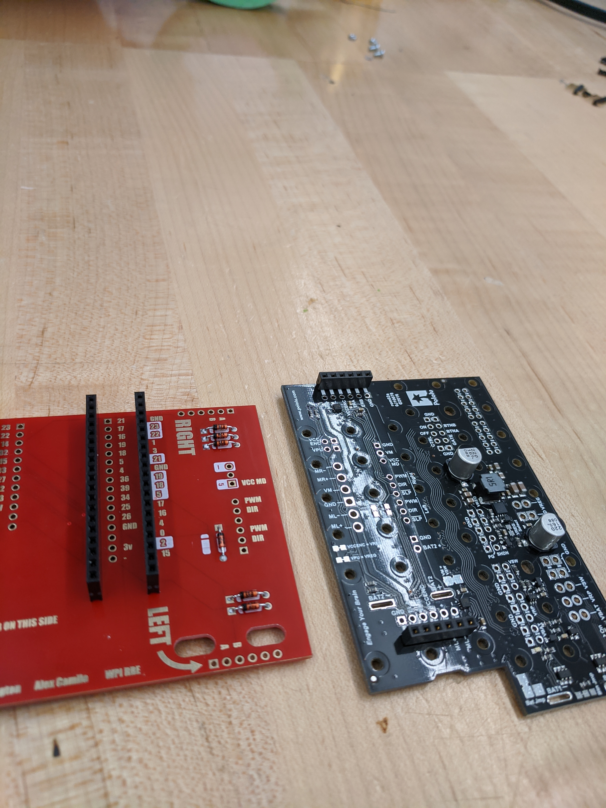
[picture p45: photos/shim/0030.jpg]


Add four sets of pins, as shown. The short leg of the pins go into the board; the long legs stick up.

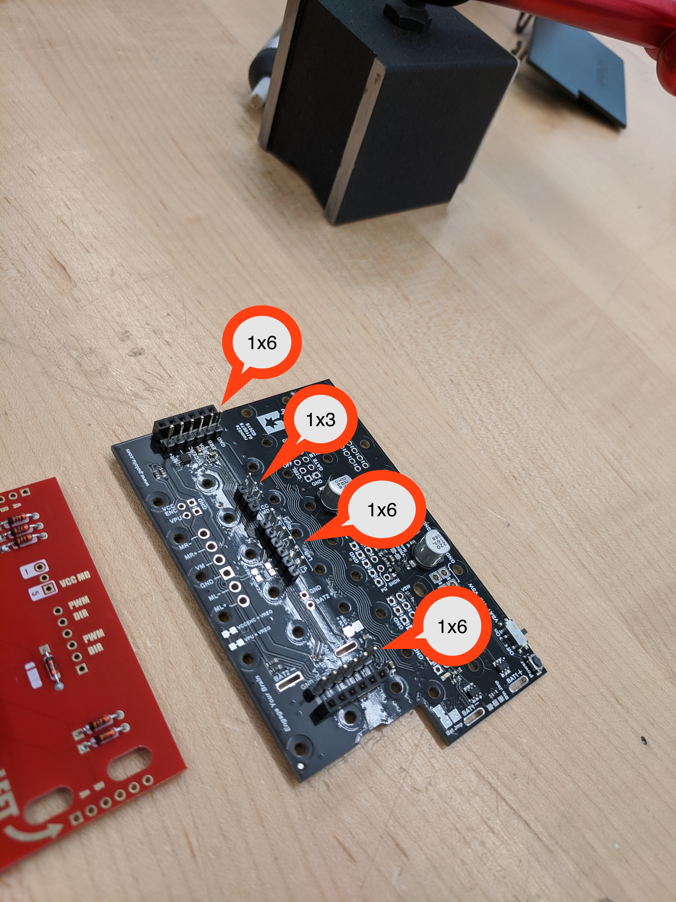
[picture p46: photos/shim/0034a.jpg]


# Step 8 Place the Shim on and tape it in place before soldering

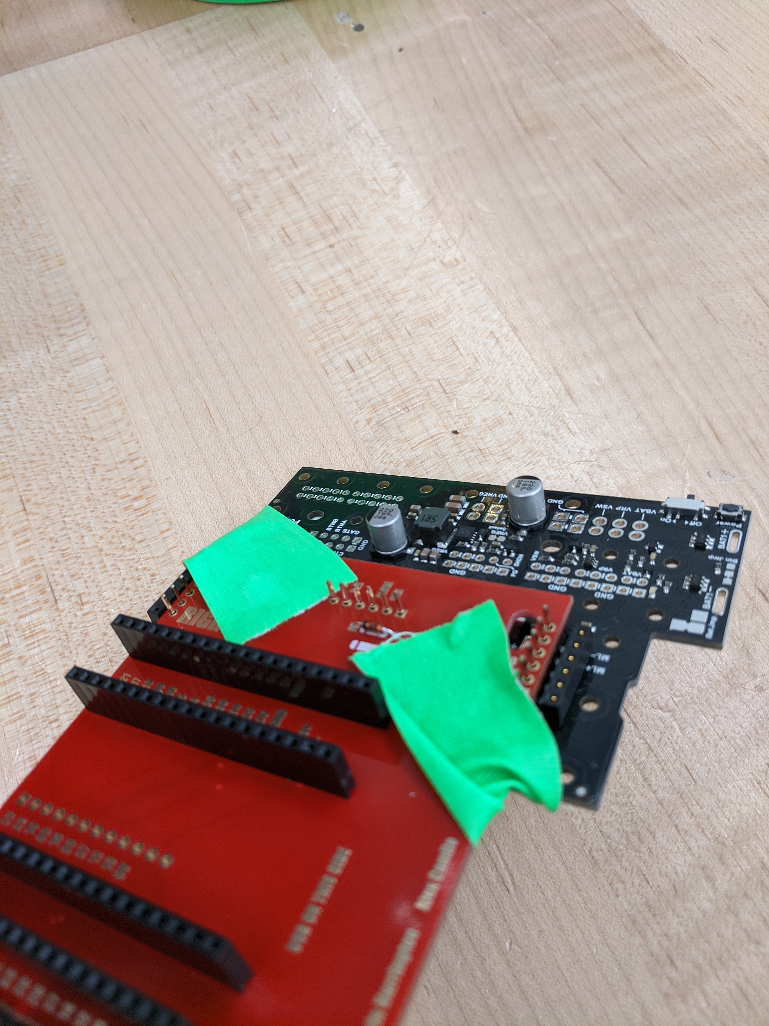
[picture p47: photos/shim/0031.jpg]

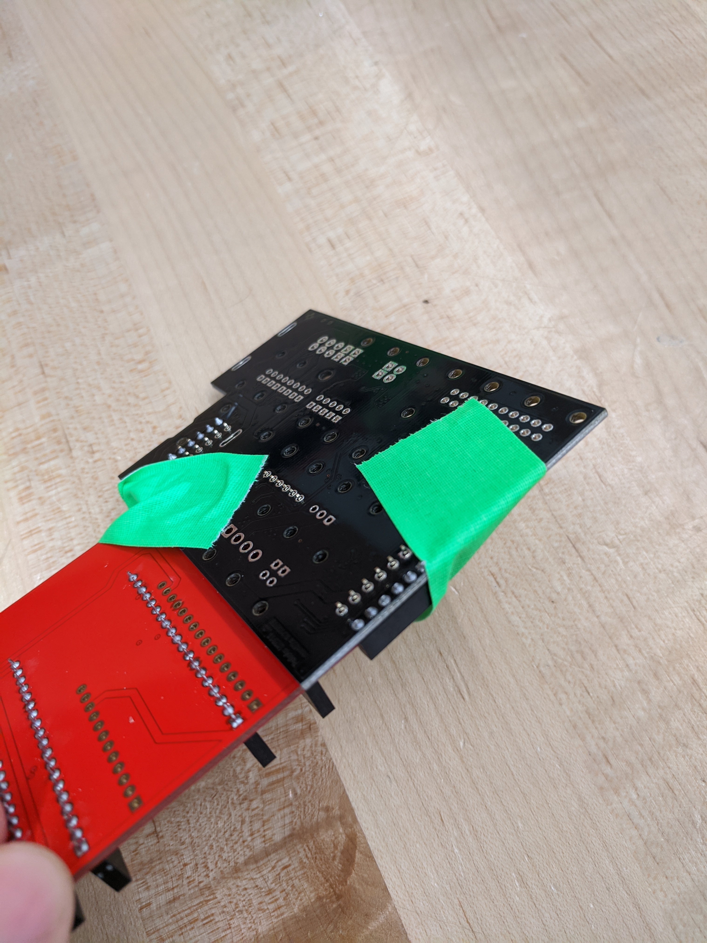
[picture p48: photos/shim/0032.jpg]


# Step 9 Solder the Driver Board ONLY (Not the red shim yet)

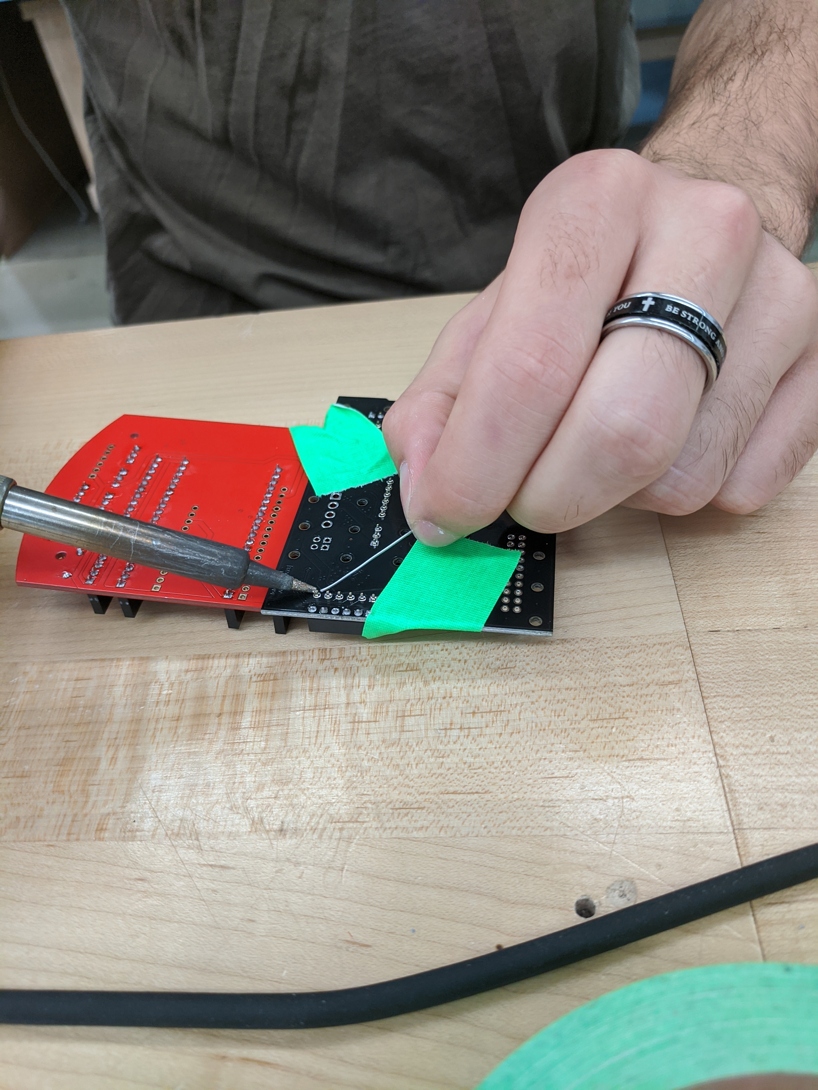
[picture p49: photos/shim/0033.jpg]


Remove the shim after soldering to check the joints

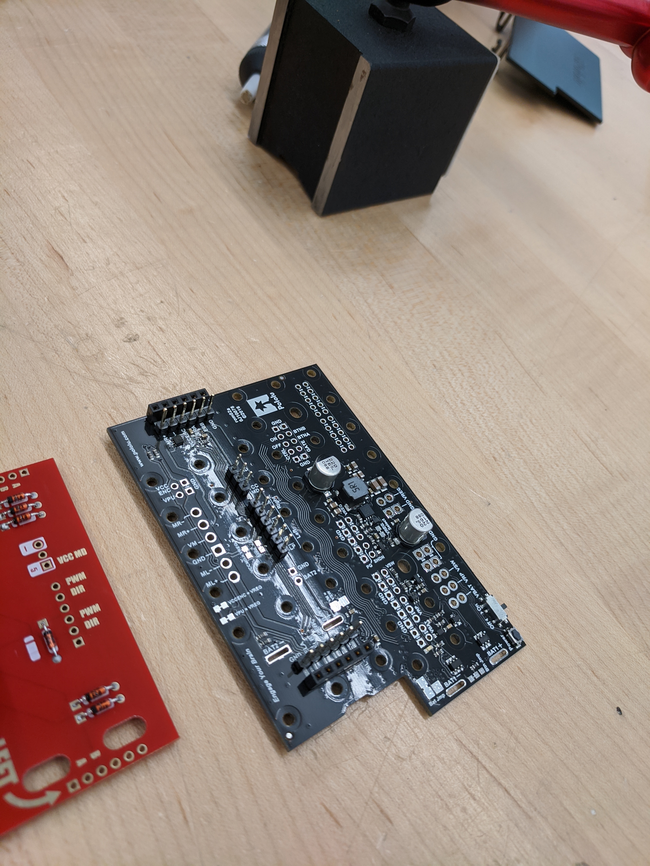
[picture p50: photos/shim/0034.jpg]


# Step 10 Add the battery tabs to the Chassis

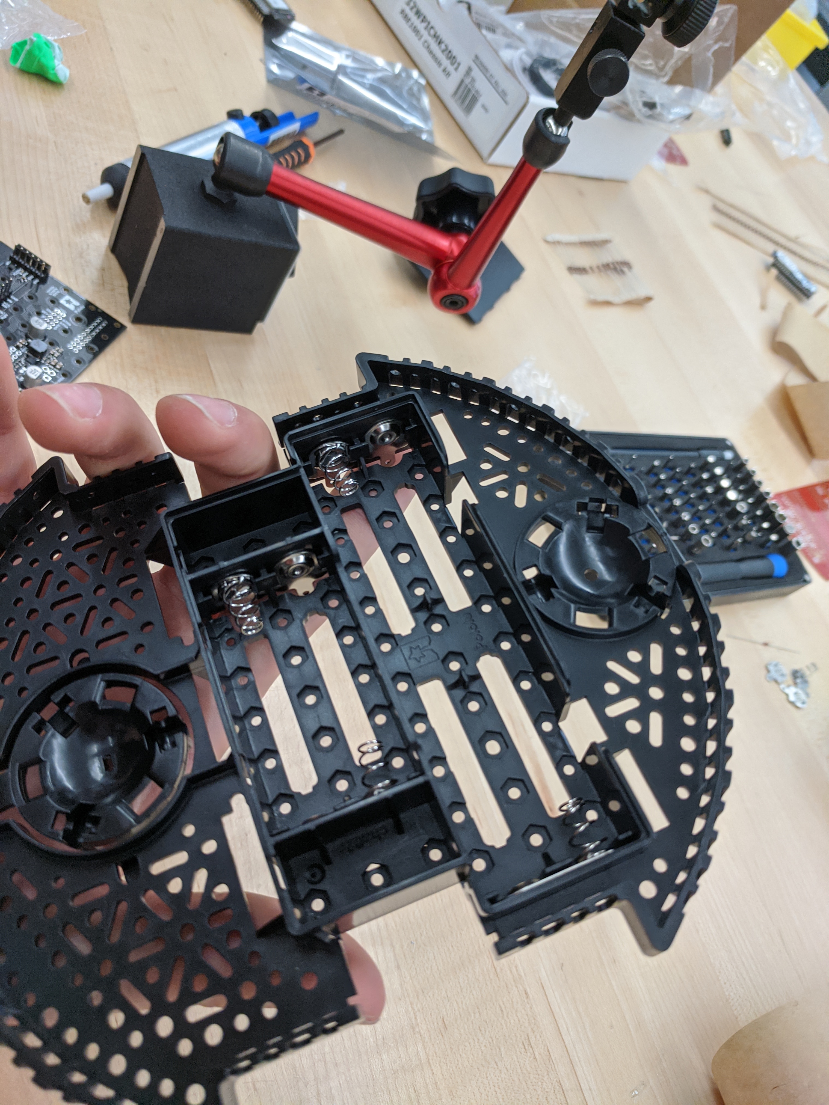
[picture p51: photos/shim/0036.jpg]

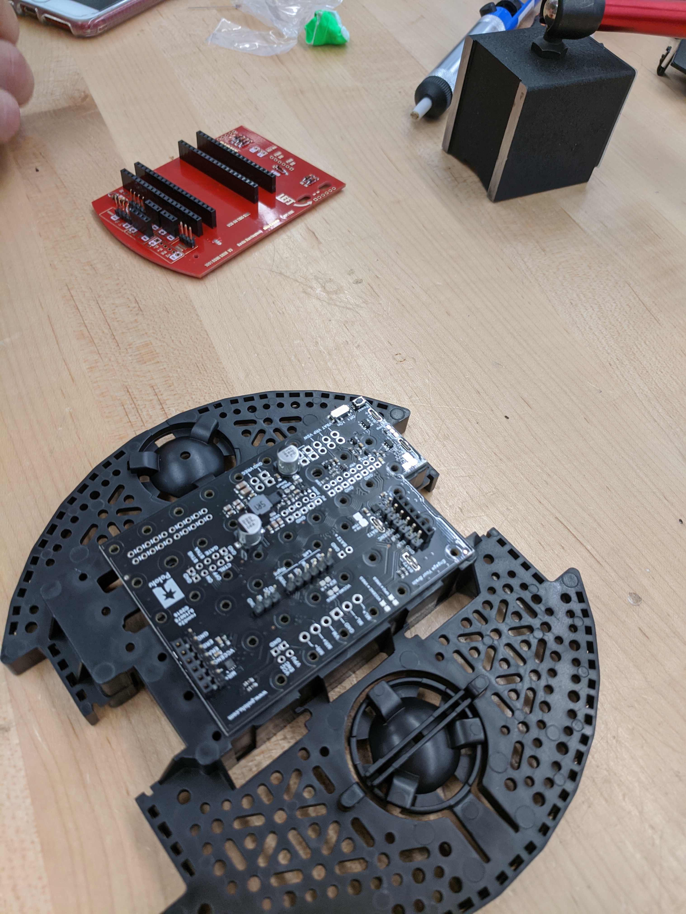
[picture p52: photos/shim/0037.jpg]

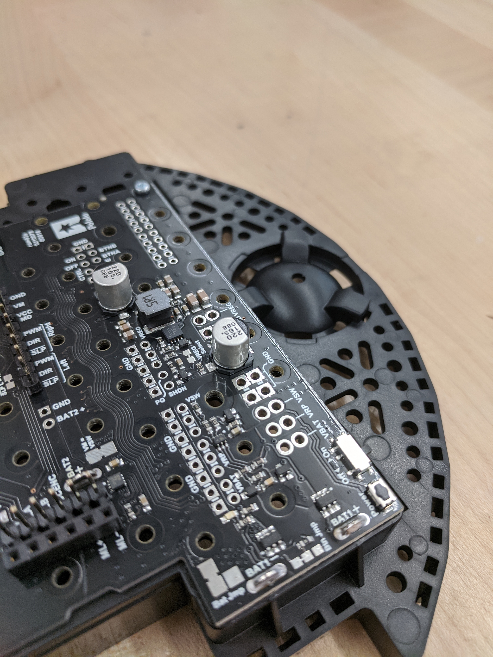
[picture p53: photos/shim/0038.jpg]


# Step 11 Solder the Battery Tabs

The tabs should protrude roughly 1/16 inch above the Driver Board.

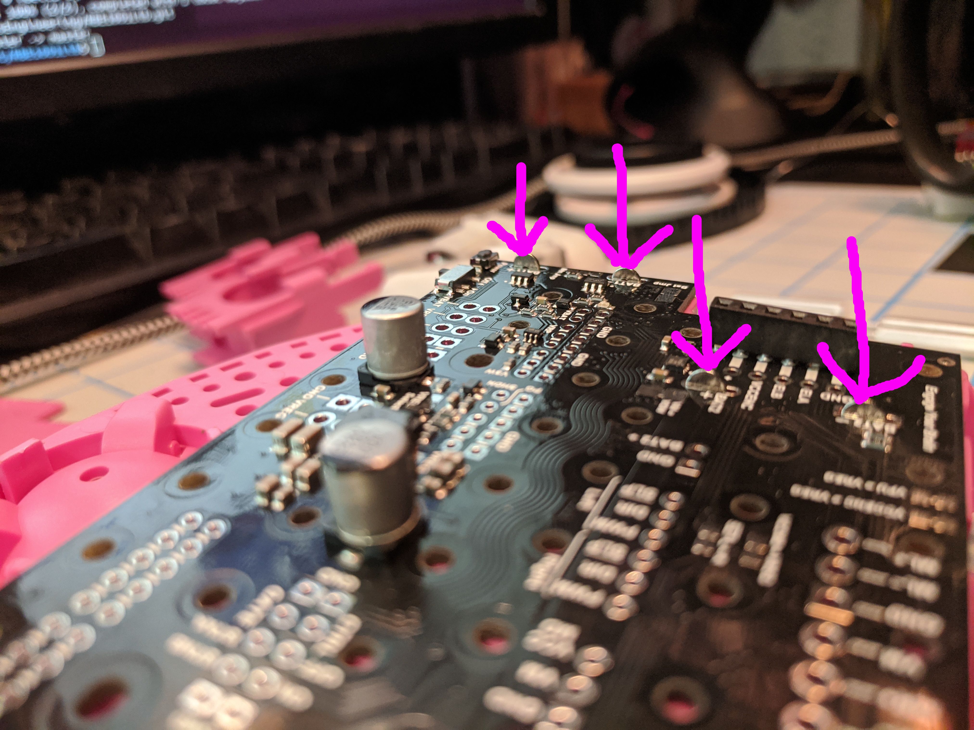
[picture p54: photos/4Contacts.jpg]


# Step 12a Add sockets to line sensor

Solder the 1x9 socket to your line sensor. The sockets go on the OPPOSITE side from the sensors, as shown.

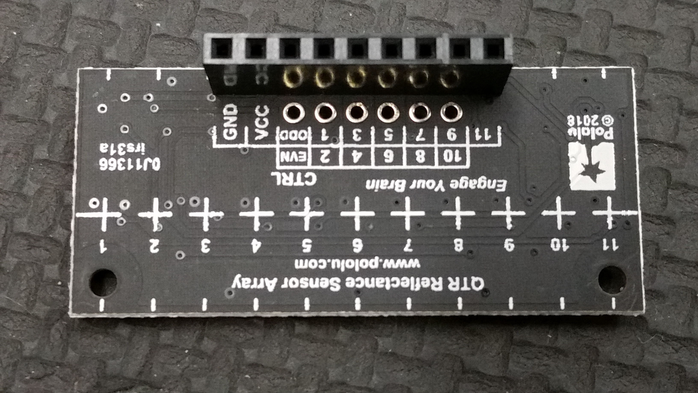
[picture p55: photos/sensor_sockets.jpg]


# Step 12b Add line sensor to chassis

Use your 3/4 inch standoffs to attach the line sensor. You'll want to do this now because it will be hard to mount the sensor after you solder in the shim.

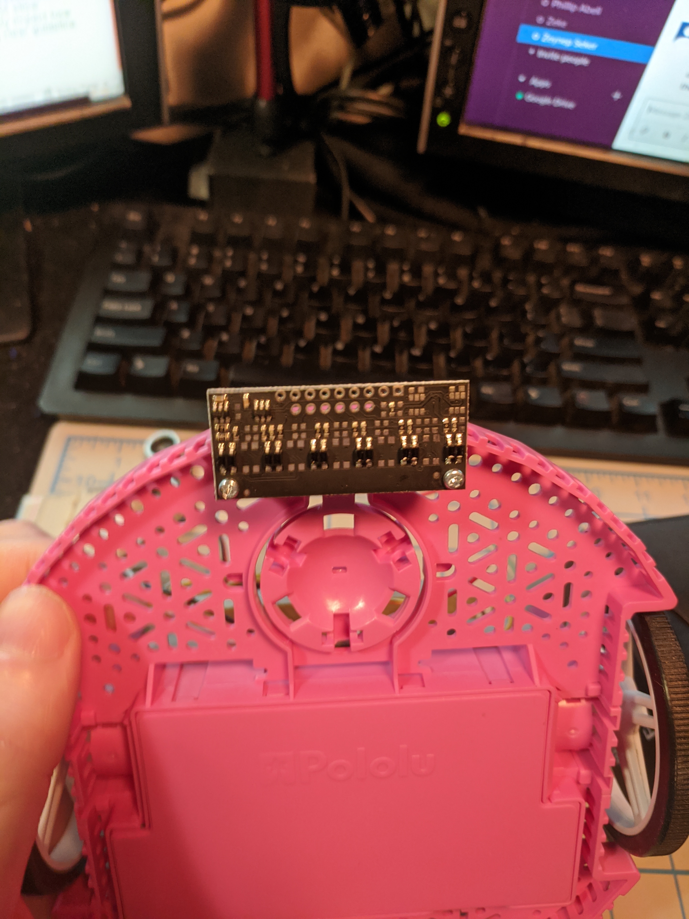
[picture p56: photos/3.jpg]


(Your sensor will have the sockets mounted.)

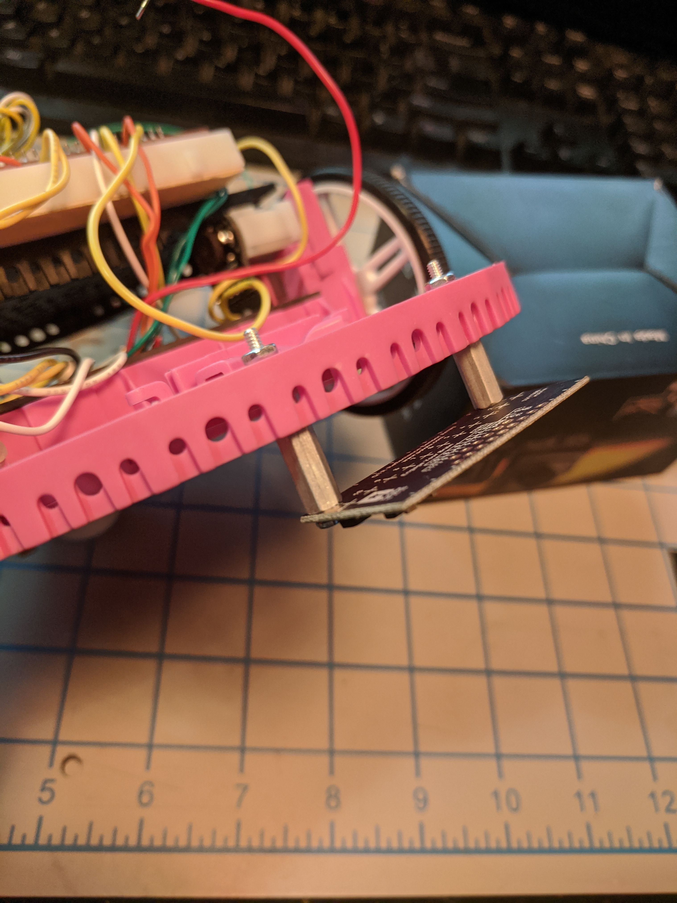
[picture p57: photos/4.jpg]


# Step 13 Solder the Shim to the Driver Board

Slip the shim board back on the pins you solder to the Driver Board in Step 9. Be sure the shim is fully seated before soldering (use tape again). The long pins will protrude well above the shim. That's OK.

# If you are in any doubt about your soldering work so far, have someone look over your soldering work (SA, LA, TA, faculty, lab manager, friends, romans, countrymen...).

Once you solder the shim board to the Driver Board, repairing bad solder joints will range from troublesome to impossible.

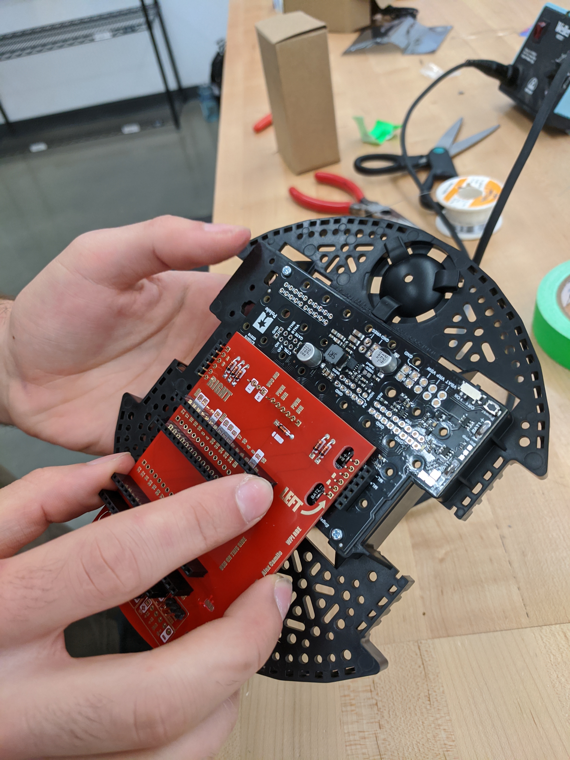
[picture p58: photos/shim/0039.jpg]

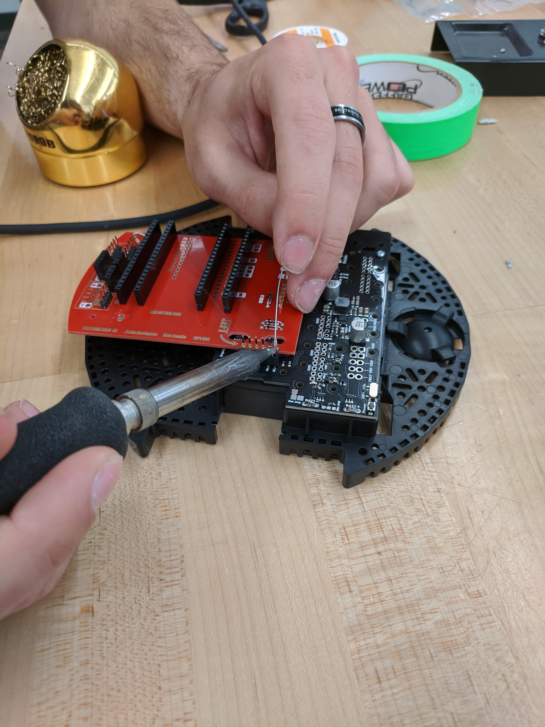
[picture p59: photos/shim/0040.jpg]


# Step 14 Add Motor Mount Clips

Add the motor Clips to both sides

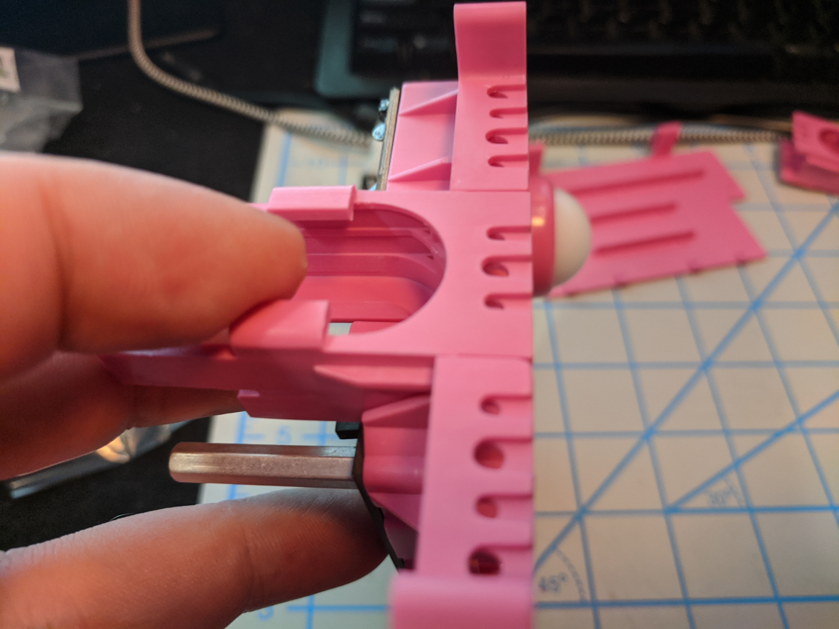
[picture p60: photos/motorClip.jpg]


Slide the motor in, being careful to get the motor pins into the receiving socket you soldered earlier:

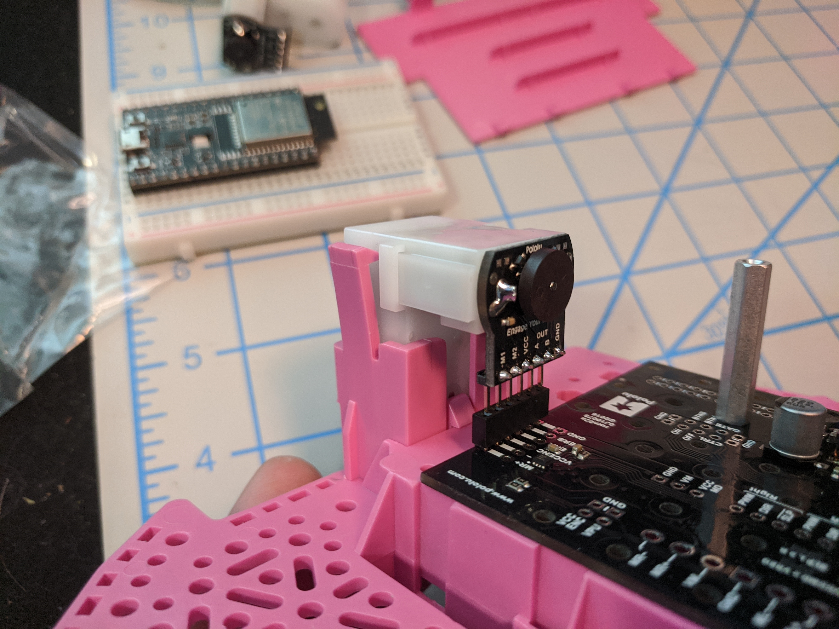
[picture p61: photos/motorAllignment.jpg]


Once aligned, fully seat the motor



Do the same for the other motor



# Step 15 Power up and test Voltages

Put your ESP32 into the sockets in the shim board. Pay close attention to orientation -- the shim has text for which end the USB connector is on. Plug in the USB cable. 

1) Check that the 5V pin is at 5 +/- 0.1 V
1) Check 3.3V pin is at 3.3 +/- 0.1 V
1) Add batteries, power on the Driver Board and unplug the USB
1) Check 5V and 3.3V pins again
 
# Step 16 Program the ESP32 with the Encoder Test Example

Under Tools -> Board select

```
ESP32 Dev Module
```

Place the jumper on the two pins marked DISABLE MOTOR (as in the front right of the picture below). This will connect the "sleep" pin to ground so your motors won't fight against you when you move them by hand.



Plug the USB back in.  

Open your IDE of choice and program the example 

```
RBE1001Lib/EncoderTest
```

Open the serial monitor after programming. Set the baud rate to "115200 baud" (in the lower right of the Serial Monitor). Gently roll the Romi forward and backward (the shim board faces the front) and verify that the wheels count up when rolling forward and down when backwards.

# Step 17 Program the ESP32 with the Motor Test Example

Open and upload the example

```
RBE1001Lib/MotorSpeedTest
```

After programming, *pick up your robot* and pull the sleep jumper out of the shim. The motors will start spinning. It may jump if there is a wiring issue, so do not do this with the robot on the table or it may drive off. Pick it up!

# Step 18 add the riser plate

Use 2x of your 1 inch standoffs to attach the riser using the recessed screws as shown. Look for the screw head near each motor. Attach the standoff below with a nut from inside the battery compartment. 

Use the 1 1/2 inch standoffs in the back to secure the back of the riser plate. 

(Ignore the wires in the picture -- this was an old version before the shim.)

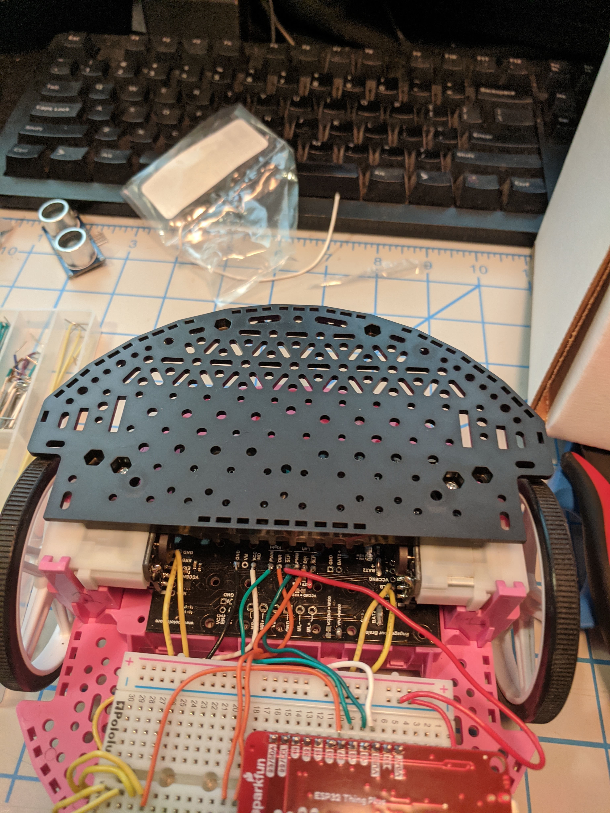
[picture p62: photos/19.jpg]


# Step 19 Add the casters

Note that the caster is "sprung" so you will probably want to push on the top of the receptacle for the caster.

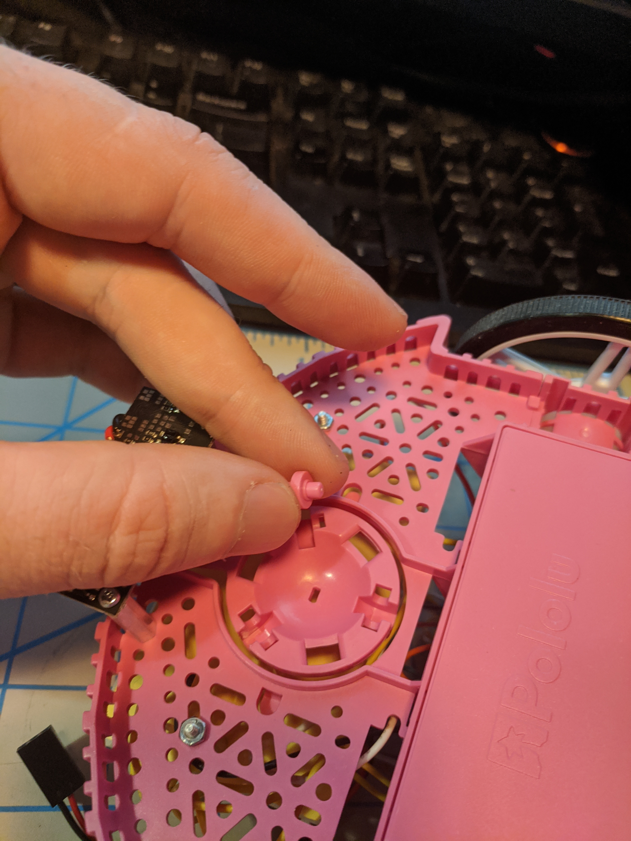
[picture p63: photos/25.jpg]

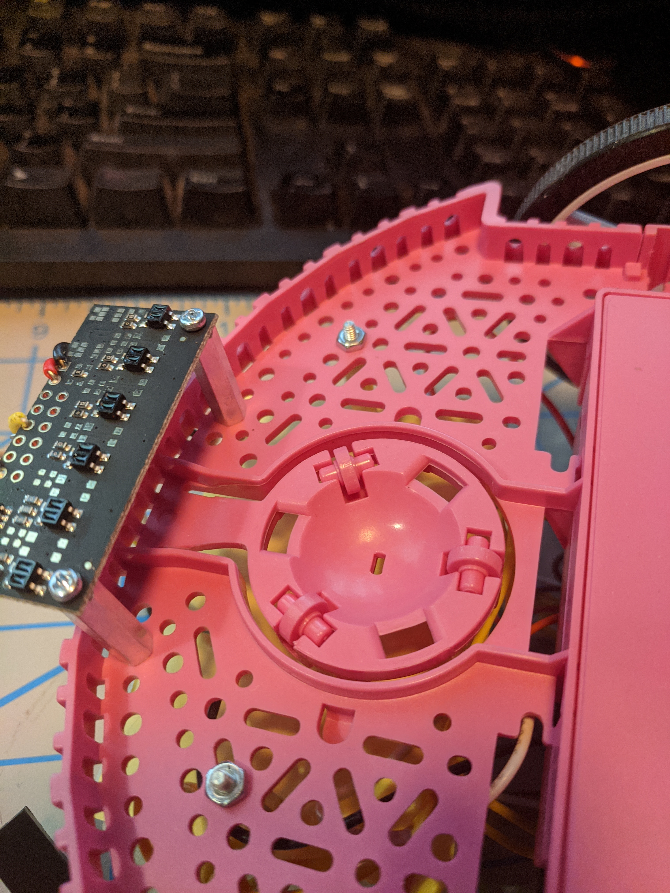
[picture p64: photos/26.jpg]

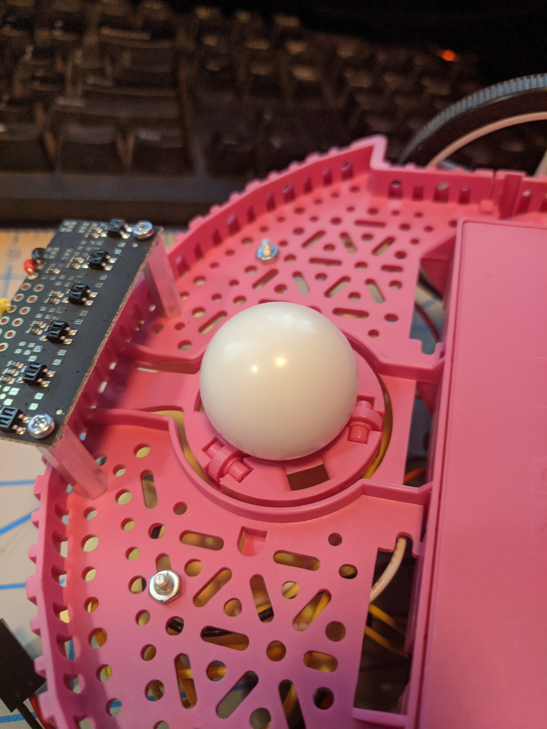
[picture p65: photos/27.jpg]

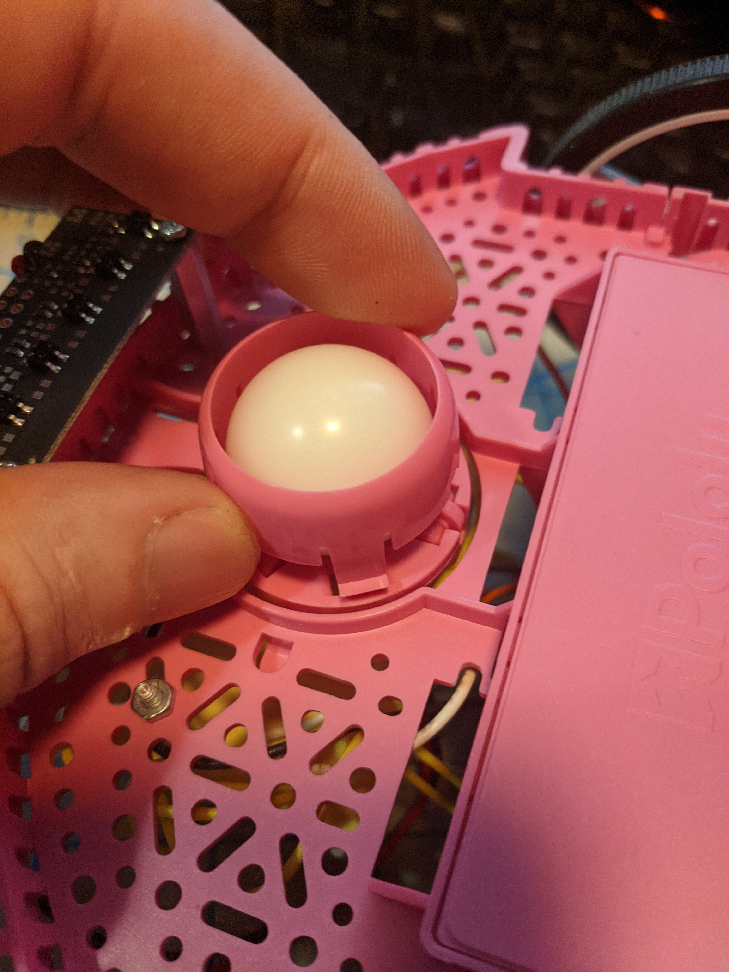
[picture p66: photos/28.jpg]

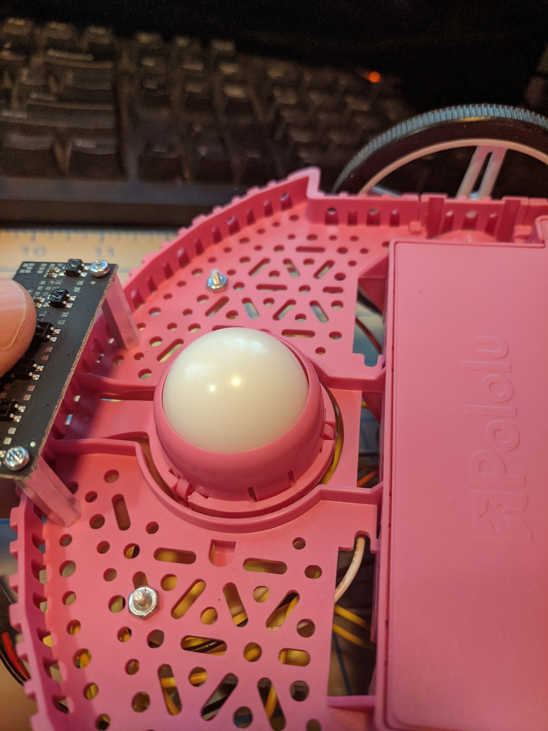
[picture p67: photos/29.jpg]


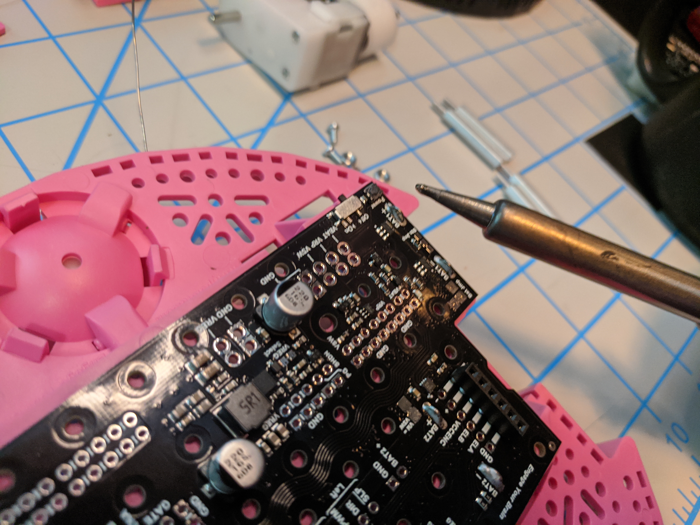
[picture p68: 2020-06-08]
photos/solderBatt.jpg

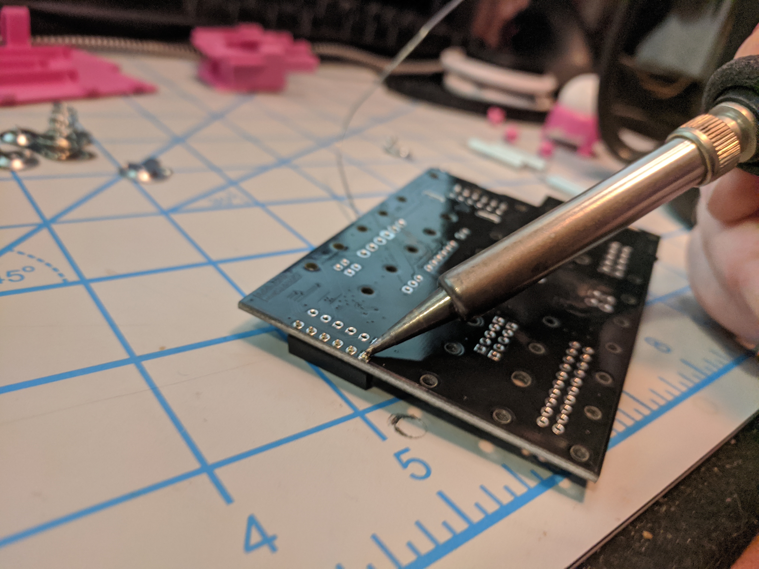
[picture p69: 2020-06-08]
photos/solderEncoderHeaders.jpg

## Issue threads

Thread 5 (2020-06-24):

Fix bom error

acamilo, 2020-06-24:
The bom lists part 3660 as a combined chassis and encoders.

The part 3660  can not be foundon pololu's website.
Please update with 2 items, The chassis kit and a set of encoders.

Closed 2020-06-24.

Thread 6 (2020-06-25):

Can you check that all the STL's are up to date?

madhephaestus, 2020-06-25:
Check what they look like in GitHub to see if it's right.

It would also be convenient if you moved all STL's into their own folder at this point (and moving forward)

nickbertozzi, 2020-06-26:
Hi Kevin,

I’m on another call till 9 AM and then will look at this.

Thanks,

Nick

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

nickbertozzi, 2020-06-26:
An STL folder has been created.  Old STLs were deleted, new ones were generated and added to the new STL folder.

nickbertozzi, 2020-06-26:
Note that we need two bushings per set.

Closed 2020-06-26.

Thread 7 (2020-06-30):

Modifications to ServoBracket

nickbertozzi, 2020-06-30:
Working on ServoBracket modifications to fit new servo.

madhephaestus, 2020-06-30:
Should i call a production hold to the older design then?

madhephaestus, 2020-06-30:
Production is held pending resolution of this ticket.

madhephaestus, 2020-06-30:
Commit the updated stl with this issue in the commit and close the issue to hand off the stl to me

nickbertozzi, 2020-06-30:
Modifications to ServoBracket completed.

Closed 2020-06-30.

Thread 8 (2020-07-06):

Adjust the bushing hole size in model

madhephaestus, 2020-07-06:
the od on the bushing for free spin is 4.85mm

the ID that it fits into is 3.95 got free spinning.

since there is more meat to work with on the brackets with holes, can you adjust the big hole and add 0.9mm to the diameter?

close with the STLs into the repo

madhephaestus, 2020-07-06:
hmm, it looks like ~0.5mm offset on both parts, which is expected on these machines. Is that in the model?

It would seem your printer @nickbertozzi  uses a much more modern slicer, using a different assumption convention than the foisie queue.

What were the true dimensions for those holes in the model? what offset was used?

Closed 2020-07-06.

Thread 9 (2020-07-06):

All #2-56 holes need offset to match production convention

madhephaestus, 2020-07-06:
The FOISIE print queue used the nozzle offset convention for critical dimensions. Models should be adjusted to match the production convention used by FOISIE

0.5mm add to outer dimensions
0.5mm removed from inner dimensions and hole diameters

Closed 2020-07-06.

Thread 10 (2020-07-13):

solder the wires before they solder the battery terminals

madhephaestus, 2020-07-13:
Wouldn’t it be easier to have them solder the wires before they solder the battery terminals? Then they can easily solder from the other side.

madhephaestus, 2020-07-13:
closed with https://github.com/WPIRoboticsEngineering/ZenRobotBuildKit/commit/5d1b8fa14f6d99a7ac269340046ae3524f7af36e

Closed 2020-07-13.

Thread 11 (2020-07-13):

Which headers are connected to the Thing board?

bradamiller, 2020-07-13:
Can you add a picture of the other side of the Thing board, I can't see what you have soldered to it.

Also, is it high enough so that there is good access to the buttons?

Closed 2020-07-13.

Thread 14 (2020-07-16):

Line sensors

gcl8a, 2020-07-16:
Assuming the interface board has the two 1x3 cxns, for the 1001 kit, it might be better to go with two of the single line sensors than the whole array. Make sure they have pins or sockets and the appropriate 3-wire cable. That both avoids soldering and keeps it all cleaner. (Soldering is not an issue, per se, but being able to remove/adjust wires would probably be a plus.)

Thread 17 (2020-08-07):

Instructions for shim board

gcl8a, 2020-08-07:
Obviously, it's on your plate, so this is a placeholder, but also questions. My plan is to solder the power board with:

- (2) 6-hole sockets for the motors
- (2) 6-pin headers in the "other" motor holes
- (1) 6-pin header for the pwm/dir/slp
- (1) 3-pin header for power

Anything else?

Then for the shim board:
- (2) 1x20(?) sockets to hold the DEV board
- (2) 1x20(?) sockets for the I/O
- (1) 1x4 pin header for the servo
- (1) 1x4 socket for the ultrasonic

Not sure about:
- line sensors
- disable motor
- there appear to be 7 spots for diodes, but I only have 6. are they all used?

Then solder the shim to the power board. Note that we have to get the shim correct before it gets soldered in, as they'll never be able to desolder that if needed. Pins and sockets would be better so they can remove the shim, if needed. Not sure if that fits with the motors.

madhephaestus, 2020-08-07:
ist 1x19 for the ESP, btw

disable motors is a 3x1 male, we provide a jumper in the kit

oops on the num of diodes, you can safely ignore the diode nearest the ESP32, thats the clamp for the servo voltage feedback, and it it redundant at this point since that sensor doesnt go high enough to be a problem

there is an unlabeled resistor also near the servo header, thats the in-line resistor for the ultrasonic

As for solder order, i reccomend soldering up the red board except all the interface pins, and then solder the interface pins while they are all loose so there is no allignment issue during assembly.

gcl8a, 2020-08-07:
What size resistor did you spec? I don’t think I got one.

Are these diodes 3.3V or 3.9V? If the latter, I’d say we use the same sized resistor as the pullups on the encoders, yes?

From my understanding of zeners, the currents are way too small to get them up near their nominal voltages. Typically, you shoot for several mA minimum, and we’re at 500 uA with a 10k pullup resistor. That would explain why a 3.9V zener is still only at ~3V.

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

madhephaestus, 2020-08-07:
i used a 10k

madhephaestus, 2020-08-07:
arg, we will need to swap the encoder lines for one of the motors in the header file to use the shim.

gcl8a, 2020-08-07:
No big deal. It’ll be a whole new term.

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

madhephaestus, 2020-08-07:
tested:
both motors and encoders
ultrasonic
servo
web control

On the SHIM board. the only error so far is the swap of the encoder pins.

Before soldering the battery tabs, the system can be tested while the solder connections are easy to get to. After the system is tested, then the driver can be soldered to the battery terminals.

gcl8a, 2020-08-09:
On mine, the ECHO pin seems to be connected directly to pin 22 on the DEV module header, in addition to pin 17 via the resistor.

Minor note: all of the diode pads are “reversed” in that the positive side is square, which is normally reserved for GND.

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

gcl8a, 2020-08-26:
My order for soldering -- which went well -- is:
- Solder all the headers and pins and diodes on the shim board EXCEPT the ones that connect it to the power board
- Solder the 1x6 motor connectors on the power board
- Put the pins in the power board and place the shim on top (for alignment)
- Solder the pins in the power board
- Remove the shim and solder the power board to the chassis (battery tabs)
- Place the shim board back on the power board and solder the pins
- You may need to slightly bend some pins so they don't interfere with the motors. Touching is OK, but they might prevent the motors from fully seating.

gcl8a, 2020-08-29:
@madhephaestus Students are getting their kits. We need final instructions for assembly.

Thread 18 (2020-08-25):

Needs to be updated, reorganized by class

gcl8a, 2020-08-25:
The BoM is confusing students as to which kits they need. It really should be organized by class.

Also, the 1001 kit doesn't have the 3d printed parts listed, nor the shim board -- in which kit to they belong?

The spring scale is way oversized. 1000g/10N should be plenty.

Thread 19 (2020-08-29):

Explanation of SLP jumper

gcl8a, 2020-08-29:
I don't have the new board. Please add a description of where to put the jumper to disable the motors. And a picture of the jumper in place.

madhephaestus, 2020-08-30:
added image https://github.com/WPIRoboticsEngineering/ZenRobotBuildKit/blob/master/photos/shim/0025.jpg to instructions with the jumper on

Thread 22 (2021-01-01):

Standoffs

gcl8a, 2021-01-01:
Need to check hardware on BoM for a complete build. I don't have an actual kit, but I used some screws and standoffs that aren't in the BoM. Most notably, (2) 1.25" standoffs for mounting the upper plate (in addition to the 1.5" standoffs that are included).

I also used several 1/2" 2-56 screws, but I think the 3/4" in the kit should be fine (and 10 should be enough). Still, someone else should do a build and count.

A second 1" 2-56 screw would be useful for the counterweight holder.

It probably isn't a bad idea to buy a 50 pack of 1" and a 100 pack of 1/2" screws.

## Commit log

2020-06-05 Chose 8mm x 6 line sensor
    Chose 6 x 8mm to give a variety of options and accommodate different tape widths, etc. It is assumed the student will only connect some of the sensors.
2020-06-08 adding encoder header solder instructions
2020-06-08 adding board so far
2020-06-08 adding more assembly instructions
2020-06-23 Cleaning out old files.
    Updating for Foisie Maker space.
    [Arm Bracket.SLDPRT, Arm Bracket.STL, Counter Balance Arm 100.SLDPRT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]
2020-06-23 Add Servo Sub Folder
    Add Servo Sub Folder
    [38 mm Standoff.SLDPRT, Arm Bracket.SLDPRT, CE3PRO_servo horn 3 v1 cover mold.3mf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]
2020-06-23 Update Link Bushing.SLDPRT
    Extended Length and decrease bushing diameter.
    [Link Bushing.SLDPRT]
2020-06-23 #4
    Made Servo Link Perpendicular to Floor
    [Servo Assembly.SLDASM]
2020-06-23 Tweeks to Several Parts
    Tweeks to dimensions on six parts and update their STL files. Deleted a few files no longer used.
    [Counter Balance Arm 100.SLDPRT, Counter Balance Arm 100.STL, Counter Balance Arm 50.SLDPRT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]
2020-06-24 adding wireing doc for sensors
2020-06-24 adding wireing instructions
2020-06-25 adding bracket
    [ultrasonicholder.stl]
2020-06-26 Created STL Folder, etc.
    Deleted old STLs and created STL folder. Generated current STL files and placed them in the STL folder.
    [Arm Bracket.STL, CE3PRO_servo horn 3 v1 cover mold.3mf, Counter Balance Arm 100.STL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]
2020-06-26 Made the two bushings separate parts
    Made the two bushings separate parts, Link Bushing_1 and Link Bushing_2.
    [Link Bushing_1.SLDPRT, Link Bushing_1.STL, Link Bushing_2.SLDPRT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]
2020-06-30 Modified ServoBracket
    Modified ServoBracket and deleted servo horn 3 v3 cover mold.stl due to changes in the new servo.
    [Servo Assembly.SLDASM, ServoBracket.SLDPRT, ServoBracket.STL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]
2020-07-06 close #8 and close #9
    Link Bushings 1 and 2: ID 2.7>3.2
    Link Bushings 1 and 2: OD 4.3>4.8
    Link Bushings 1 and 2: Length 4.6>6.1
    Servo Link: ID 4.6>6.0
    Servo Link: Height 10>12
    Servo Bracket: Holes for Servo 2.7>3.1
    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
    [Arm Bracket.SLDPRT, Arm Bracket.STL, Counter Balance Arm 100.SLDPRT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]
2020-07-11 Alternative connector for Sharp IR
2020-07-13 Updated battery terminal instructions.
2020-07-13 Board advice
2020-07-13 Only 1 ~SLP cxn needed; warnings for motors
2020-07-13 Added soldering tutorial link
2020-07-15 Clarity for 1x6 sockets
2020-07-16 swapped encoder lines on Right motor
2020-07-20 Deleted image of incorrect encoder wiring.
2020-08-12 Updated socket counts
2020-08-17 move ultrasoniuc holder
    [ultrasonicholder.stl]
2020-08-21 Added screw terminal for blue motor
2020-08-21 Added LED and resistor
2020-08-26 update sensor wires
2020-08-29 Skip Step 12 -- needs sockets.
    The sensor array will be wired with sockets.
2020-08-29 Ignore wires in Step 18
2020-08-29 sensor sockets
2020-08-29 Added picture of sensor with sockets.
2020-08-29 annotated resistor
2020-08-29 annotated resistor in Step 2
2020-08-30 Removed battery tabs.
2020-08-31 moved 1k resistor to ESP32 kit
2020-08-31 1k resistor
2020-09-02 adding board selection
2020-09-13 ultrasonic instructions
2020-09-13 line sensors
2020-09-13 Restored sensor wiring with new page
2020-09-22 Fix spelling in wireSensors.md
2020-11-10 Tentative ToF sensor
2021-02-17 updated line sensor for new board
2021-02-17 more new board
